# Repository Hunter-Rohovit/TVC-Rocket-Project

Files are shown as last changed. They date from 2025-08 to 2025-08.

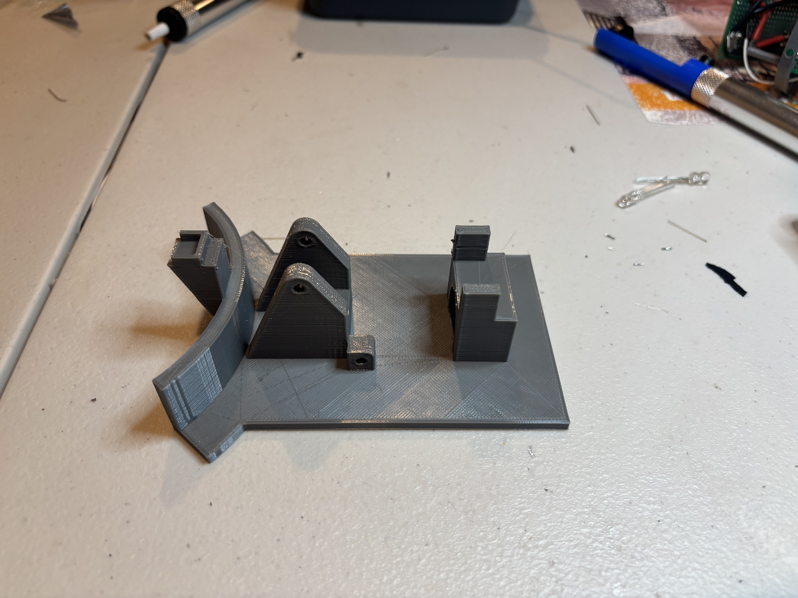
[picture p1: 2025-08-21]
Pictures_Videos/Launch Pad Assembly/IMG_3920.jpg

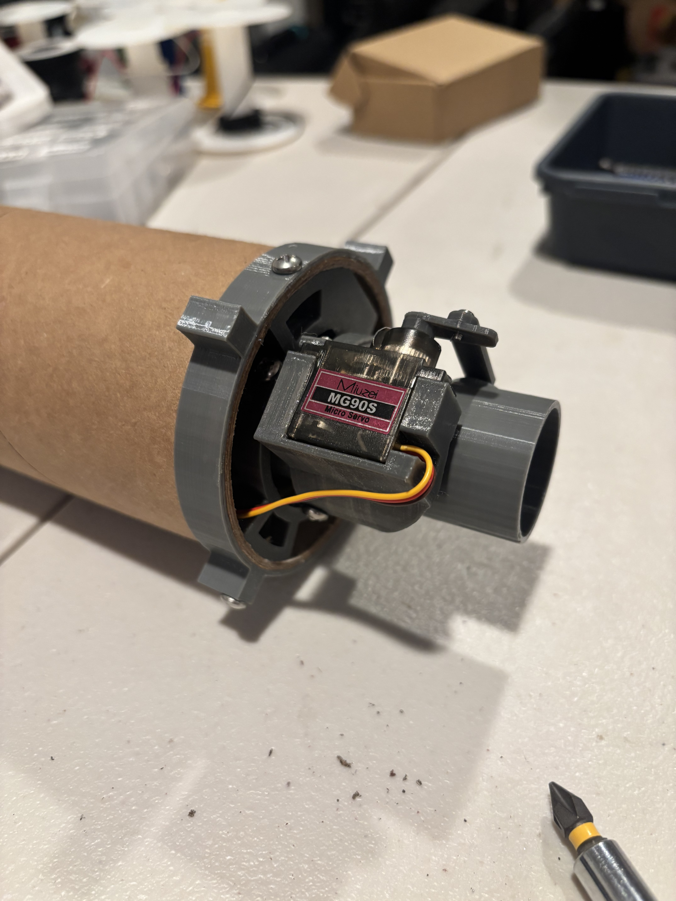
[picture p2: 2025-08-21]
Pictures_Videos/First Prototype Assembly/IMG_3949.jpg

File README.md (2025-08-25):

# Finless Thrust Vector Controlled Rocket
This page details the progress I have made in developing an autonomous Thrust Vector Controlled Model Rocket. This project was inspired by Joe Barnard at BPS Space, with his launching and landing of model rockets, as well as my own interest in Aerospace & Controls Engineering. It is a continuation of a project that began last summer (2024), where I designed the first prototype of a gimbal mount and ran a couple of tests while firing a motor. [Link](https://github.com/Hunter-Rohovit/TVC-Gimbal-Mount). All the work shown here was done over this summer (2025).

## Sections of this page:
1. [Overview](#overview)  
2. [CAD](#cad)  
3. [Avionics](#avionics)  
4. [Gimbal Mount](#gimbal-mount)  
5. [Servo Characterization](#servo-characterization)  
6. [Experimental Tests](#experimental-tests)  
7. [Computational Fluid Dynamics](#computational-fluid-dynamics)  
8. [6DoF Simulation in MATLAB](#6dof-simulation-in-matlab)  
9. [Control Algorithm](#control-algorithm)  
10. [Parachute Ejection & Recovery System](#parachute-ejection--recovery-system)  
11. [Launch Pad](#custom-launch-pad)

IMG_6904 (1)

---

## Overview
The goal of this project was to design, simulate, and build a finless rocket capable of stabilizing itself through thrust vectoring. This project integrates mechanical design, electronics, control theory, simulation, and experimental testing into a single system. Unfortunately, as the summer came to a close, I fell short of a first launch attempt by a couple of weeks. However, I made significant progress towards the eventual goal of launch and stable flight. Here's an overview of key accomplishments from this project so far: 
- Finalized design of gimbal mount and decreased thrust vector step size down to 0.2 degrees compared with the first prototype's step size of 0.75 degrees.
- Designed and assembled a custom flight computer Printed Circuit Board (PCB) consisting of a micro controller, Inertial Measurement Unit, Barometer Module, Data Storage, LoRa telemetry, and a MOSFET pyro channel.
- Used Solidworks CAD to design the rocket from scratch, integrating 3D printed mounts and other subsystems on the rocket.
- Developed a piston ejection system using 4Fg Black Powder for reliable deployment of parachutes.
- Designed and built a parachute to safely recover the vehicle during descent.
- Designed a custom Launch Pad with servo-driven quick-release Clamps, ignition circuit, and a custom Launch Pad PCB capable of controlling systems and transceiving radio commands.
- Computationally estimated and experimentally measured the rocket's Center of Gravity and Moment of Inertia about its lateral axes.
- Experimentally measured and analyzed servo motor hysteresis, latency, and response lag to accurately model gimbal mount dynamics.
- Formulated a nonlinear state-space representation of the rocket's rotational and translational dynamics in MATLAB.
- Built a full 6DoF state-space model of the rocket in MATLAB, integrating aerodynamic forces & moments, thrust vectoring, and environmental factors.
- Used Ansys Fluent's Computational Fluid Dynamics to determine lift and drag coefficients, aerodynamic moments, and center of pressure at various angles of attack to be used in 6DoF Simulation.
- Developed the structure of a Simulink Model integrating the 6DoF MATLAB function, a cascading PID Loop, and servo dynamics for accurate simulation and tuning of controller.
- Performed preliminary tuning and adjustment of PID gains of both inner and outer loops.
- Used C++ to program fundamental systems and tests of the Flight Computer, Launch Pad Computer, and Ground Station.

## CAD
Everything that was physically built was designed in Solidworks CAD beforehand. This includes the rocket, launch pad, and test stand. 
### Rocket
[Link To Onshape CAD Model of Rocket](https://cad.onshape.com/documents/63a8c4b73cd8738e99a4bd5d/w/619c465f67d6cd9f3f21c386/e/602e70b6c7c6c566dec7f707)


### Launch Pad
[Link To Onshape CAD Model of Launch Pad](https://cad.onshape.com/documents/538db86218341a015942f826/w/e10a91c609211941c8562602/e/c57fd2841c9af4f969e365a8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)


## Avionics
There were two custom Printed Circuit Boards built for this project. The first was for the flight computer and the second was for the launch pad computer. 
### Flight Computer
The flight computer consisted of a Teensy 4.0 Microcontroller, 5V and 3.3V Pololu Buck Converters, BNO085 Inertial Measurement Unit, BMP388 Barometer, SPI Flash SD, RFM95W Radio Transceiver, LED, Buzzer, external micro SD breakout, screw terminals for servo outputs, and a MOSFET circuit for a pyrotechnic ignition channel. I2C communication was primarily used for simplicity, though SPI communication was used for some devices.
#### Block Diagram
<p align="center">
  
</p>

#### Altium PCB Designer & Assembled PCB
<p align="center">
  
  
</p>

### Launch Pad Computer
The Launch Pad Computer consisted of a Teensy 4.0 Microcontroller, 5V Pololu Buck Converter, RFM95W Radio Transceiver, LEDs, Buzzer, 6 screw terminals for servo control (extra 2 for redundancy), 3 MOSFET circuits connected to Igniter Channels (2 extra channels for redundancy as well). 
#### Block Diagram
<p align="center">
  
</p>

#### Altium PCB Designer & Assembled PCB
<p align="center">
  
  
</p>

## Gimbal Mount
Having a robust gimbal mount that can effectively vector thrust is key to the success of this project, which is why I spent an entire summer dedicated just to it. The gimbal mount is controlled by two servo motors each connected to linkage mechanisms. There are two "loops". The inner loop is connected to the rocket motor case at a pivot, allowing the inner servo motor to rotate the motor case back and forth. The entire inner loop is connected to the outer loop by a pivot. The servo motor on the outer loop moves the inner loop back and forth in a direction perpendicular to the inner servo to allow vectoring in two directions. This mount has maximum and minimum vector angles of 4.5 degrees in both the pitch and yaw directions. 

While the final design of the gimbal mount is the same as the first prototypes in terms of how it vectors the thrust, these were some key changes made to improve the overall design:
- Shortened distance between control horn pivot and linkage connection.
- Increased distance between linkage connection and motor case/inner loop pivot.
- Increased support on inner and outer loops for more rigidity.
  
These three changes increased servo resolution and decreased flex in the mount. For more info, look at "Old TVC Mount Issues" folder.
[Link to Onshape CAD for Gimbal Mount](https://cad.onshape.com/documents/97e67a90e16df294bea9c07c/w/7f59de1ae6b53eca2492785b/e/3da8b51d2cceb306dbc743ae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)
<p align="center">
  
  
  
  
</p>

## Servo Characterization
In order to accurately represent the dynamics of the gimbal mount I needed an in depth understanding of how it moves when I command it to certain angles. This was one part of the project I hadn't anticipated needing to do, but as I began developing the Simulink Model, I realized it was very important. There are four characteristics of the servo I needed to understand it's dynamics:
1. Hysteresis (servos behave differently when commanded in different directions)
2. Latency (how much time it takes for the servo to begin moving once the command is called)
3. Response Lag (How long it takes for the servo to move to it's final position once the command is called)

### Servo Hysteresis
To accurately model this, I ran multiple tests increasing the servo angle from -22 to +22 degrees (max range of gimbal mount, corresponds to ~4.5 degrees actual) and decreasing from +22 to -22 degrees. 
I recorded the commanded angles and true angles and plotted them on graphs using MATLAB. I repeated this several times for both pitch and yaw axes. I then fitted a polynomial to the data. 
<p align="center">
  
  
  
  
</p>

### Servo Latency & Response Lag
To find these two values I used a camera to capture the motion of the gimbal mount. When I sent the signal to the servo motor, I simultaneously turned on the LED on the Flight Computer, so I could visually record the time stamp when command sent. From there I recorded the time stamp where the gimbal mount began moving (Latency) and recorded the time stamp where the gimbal mount stopped it's movement (Response Lag). I counted the number of frames between these three time stamps and divided by the frame rate to get the actual time. I repeated this for multiple tests to get several values at different angles.
<p align="center">
  
  
</p>

## Experimental Tests
To further understand the system, two important values needed to be found: the Center of Gravity and the Moment of Inertia about the lateral axes. I had estimated these values using Solidworks CG locator by overwriting the material density, finding the CG of each individual part, and finding their distance from the nose tip. However, the physical tests account for additional fasteners, glue, and wires that I didn't account for in the calculation, making it more accurate. 
### Center of Gravity
Finding the center of gravity was relatively simple. I hung a string and created a loop for the rocket to be placed. I shifted the rocket around until it was able to balance by itself and labeled that point the CG. 


### Moment of Inertia
To find the Moment of Inertia I used the Bifilar Pendulum Test. I hung two lines and attached them to the rocket 40 inches apart and centered about the CG, and recorded those measurements. I then rotated the rocket and started a timer as soon as I let go. After 10 oscillations, I recorded the time, to get the period of oscillation, and repeated this for multiple tests. From there, I could derive the Moment of Inertia from the mass of hte rocket, the length of the string, the distance between the two points, and the period time. I assumed the rocket to be symmetric about the longitudinal axis, so I only found one moment of inertia and used the same values for both Iy and Iz (pitch & yaw axes). I didn't find the roll Moment of Inertia as I could only control Pitcha and Yaw with Thrust Vectoring, and there wouldn't be any significant torques acting to roll the rocket. I still estimated it through a calculation, to be used in the 6DoF simulation.  
IMG_4121 (1)

## Computational Fluid Dynamics
Used Ansys Fluent CFD to deteremine coefficients of forces, moments, and the location of center of pressure at various angles of attack. Generated lift, drag, and moment coefficient curves across 0-90 degrees angle of attack. This data along with estimations for the aerodynamic damping derivative (derived from CFD results) was implemented into the MATLAB 6DoF function. For Lift and Drag Coefficients, Ansys was used to find the magnitude of these forces at 40m/s, which could then be used to solve for Cd x ReferenceArea and Cl x ReferenceArea rather than needing to calculate both Cd/Cl and reference area at different angles of attack. The static moment was normalized for velocity and CP location relative to CG. The center of pressure was defined from the nose tip and was calculated through dividing the static moment by the normal force to get the distance from CG. 

### 2D Simulation Velocity Contour
Ansys_Contour_Screenshot

### 3D Simulation Static Pressure Contour
Static Pressure Contour CFD

### CFD Results
<p align="center">
  
  
  
  
</p>

## 6DoF Simulation in MATLAB
Developed the equations for state space estimation and built a six-degree-of-freedom function in MATLAB to compute the time derivative of the rocket's 6DoF state. The state equation was formulated using quaternions and angular velocity for rotational motion, as well as inertial position and velocity to represent the rocket's translational motion. The choice of using quaternions over traditional euler angles was to prevent gimbal lock in the simulation. This function uses control inputs (vector angles), thrust data, aerodynamic data, and environmental conditions to estimate the translational and rotational acceleration. Aerodynamic forces and moments are computed in the body reference frame, then transformed into the inertial frame to integrate the full equations of motion. This simulation is fundamental to the development of the control algorithm and generation of flight profiles. 

### Visualization of Forces, Moments, and Axes 


## Control Algorithm
To develop the control algorithm I used Simulink to create a closed-loop model that integrates the 6DoF simulation from above and servo dynamics. The controller is structured as a cascaded PI-PID controller. The outer PI loop computes error based on attitude, and then outputs a desired angular rate. The inner loop then uses that output and the measured actual angular rate to calculate the error and generates commanded pitch and yaw outputs. The decision to use a PI rather than PID controller for the outer loop was based off the fact that the derivative of attitude error is angular rate, which is already being regulated in the inner loop. These commands then pass through a section that encapsulates the experimentally derived servo dynamics to feed the true thrust vector angles back into the process section. These were the Simulink Blocks used to model servo dynamics:
- Dead Zone: Very small changes to servo angle will not result in any change in servo position.
- Saturation: Maximum and minimum gimbal angles.
- Rate Limiter: Rising and falling slew rate of servo motor (maximum angular rate of motor).
- Transport Delay: Modeled servo latency
- Transfer Function: Used for servo response lag (the time to move from initial to final position)
- True Gimbal Function: Determines whether servo is moving up or down, and uses servo hysteresis data to ouput actual gimbal
- Zero-Order Hold: Models refresh rate of Inertial Measurement Unit (400hz)

Controller Tuning Strategy:
I have already completed preliminary tuning of this control algorithm, but some refinement is still needed. I started with the inner loop and then moved onto the outer loop, once the angular velocity showed convergence. The general strategy I used to tune both loops was to start with low Proportional gain and increase until I saw adequate response. If there were large-amplitude oscillations I increased the derivative gain, until it was less severe. If there was any steady-state offset I increased the integral gain. For both loops, I tuned one axis at a time, independently of one another. After, I modified the gains slightly when incorporating pitch and yaw together. In the future, I plan to add derivative filtering to the inner PID loop to prevent sharp spikes in commanded angles, and reduce the noise in the servo outputs.

### Simulink Model


### Scope Output

Example output including angular velocity, quaternions, desired pitch rate, commanded pitch rate. These scopes are what allowed visual tuning of the gains. There's significant noise in the commanded pitch angle showing the need for derivative filtering. 

## Parachute Ejection & Recovery System
The parachute ejection system on the TVC model rocket is a custom built piston ejection device. At the bottom of this system is the piston canister bulkhead. It is what stores the FFFFg black powder and the e-matches used to ignite it. The high pressure created by the ignition gases pushes out the piston cap, which in turn also pushes out the shock cord, parachute, and nosecone. This ejection method is significantly more reliable and easier to implement than a mechanical deployment device. It's also a lot lighter, helping with total mass reduction. The electronics are very simple, only requiring a single MOSFET pyro channel. For recovery, the parachute was designed for a 1kg rocket (actual mass is ~850g) to land at a velocity of 4m/s. It's made of ripstop nylon fabric, which is very strong and ligthweight. Attached to the shroud lines is a swivel to reduce the chances of lines tangling. Here's a video of the parachute ejection test: [Ejection Test](https://github.com/Hunter-Rohovit/TVC-Rocket-Project/blob/main/Pictures_Videos/Rocket%20Systems%20Tests/Parachute_Ejection_Test.mov)      
### Recovery System

### Assembly
<p align="center">
  
  
  
  
</p>

## Custom Launch Pad
The custom designed launch pad is composed of a spring loaded clamp release mechanism, a custom launch pad computer, and ignition circuit. In the secured position, the four clamps lock down onto the rocket's launch pad mount. Shortly after rocket motor ignition, the servo motors rotate and hit the release arms out from underneath the clamps, allowing the springs to snap downward. This design ensures the clamps retract quickly and remain out of the rocket's path. Here's a video releasing the launch clamps: [Launch Clamp Test](https://github.com/Hunter-Rohovit/TVC-Rocket-Project/blob/main/Pictures_Videos/Rocket%20Systems%20Tests/LaunchPadTest.mov)

### Clamped Position


### Open Position


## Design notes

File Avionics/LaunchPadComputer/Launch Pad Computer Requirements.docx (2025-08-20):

Purpose of the Launch Pad Computer:

- Remotely communicate with the rocket’s on board flight computer
- Remotely communicate with laptop ground station
- Fire rocket motor igniter
- Control servo motors for launch clamps

Needs of Launch Pad Computer:

- Microcontroller
- LoRa Radio Transceiver
- At least 2-3 MOSFET igniter circuits for redundancy
- 14.7V battery (what I have available already)
- 5V regulator for Teensy 4.0 and servo motors (must be capable of handing max stall current of 4 servo motors)
- Current regulation for firstfire mini motor starters (>3A)
- Pull down resistors on MOSFET circuits to prevent accidental firing
- Redundant arm switch

Resistor needed for the igniter circuit:

- Battery – 14.7V
- Recommended voltage: 12V
- Recommended current: >3A
- Using a 3.9 ohm resistor: 14.7/3.9 = 3.8 amps
- Power Dissipated: P=I^2*R = (3.8amps)^2*3.9ohms = 56W
  - Need a 3.9ohm resistor with high power dissipation (at least 60W)
  - https://www.digikey.com/en/products/detail/te-connectivity-passive-product/TE60B3R9J/2367245

Max Current Draw:

- Igniter: 2-5A
- Teensy 4.0: 250mA
- LoRa FRM95W radio: 100mA
- 4x MG90S servo: 900mA each

5V Regulator:

- Total current draw: 250mA+100Ma+900x4 mA = 3.95A
- It should be rated to 5A
- https://www.pololu.com/product/2851

Capacitors:

- The purpose for the capacitors on the MOSFET Igniter Circuits is to act as local energy reservoirs and avoid voltage dips when driving high current loads (e-match)
  - I chose 470 microfarad electrolytic capacitors based on the physical size of the capacitor and what I had available
  - Because the battery will be driving most of the current, I don’t need a super large capacitor, which is why 470 microfarads was good for what I needed
- The capacitors connected close to the servos are 220 microfarad capacitors
  - They serve a very similar purpose to prevent voltage dips and ensure the servos have enough power to be actuated all at the same time to release the launch clamps
- I could have done the actual calculation based on the allowable voltage drop using this equation: Voltage = I*dt/C or based on E=1/2*C*V^2
  - However, considering the energy required is an arbitrary value depending on how much is supplied by the battery, I decided not to use these equations to size the capacitors

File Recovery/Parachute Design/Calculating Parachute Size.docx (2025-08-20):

The main parameter I am designing around with the parachute is descent speed. Parachutes reach terminal velocity where the drag force from the parachute is equal to the dry weight of the rocket after burnout. We can use the drag force equation:

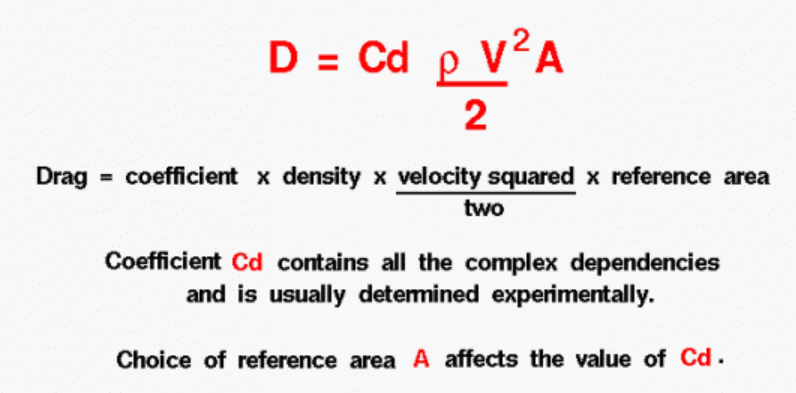
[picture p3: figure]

Coefficient of Drag for model rocket parachutes is estimated at 0.75 as per:

https://apogeerockets.com/education/downloads/Newsletter149.pdf

https://www.grc.nasa.gov/www/k-12/VirtualAero/BottleRocket/airplane/rktvrecv

The density of air at sea level ~1.225 kg/m^3.

Typical safe landing velocities are generally less than 6m/s. Apogee recommends 3.5-4.5 m/s.

- The decision for landing speed ultimately comes down to being soft enough to safely touch down without damaging any flight hardware while being small enough so that it doesn’t introduce any significant amount of mass.

The required drag force is equal to the force of gravity of the rocket, which we can calculate from the mass of the rocket. From there, the area of the parachute can be calculated.

It’s important to note that the area of the parachute should be the projected area not the surface area. However, these areas often do not vary by much and can be assumed to be the same.

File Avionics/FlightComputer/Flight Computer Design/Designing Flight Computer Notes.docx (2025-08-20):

- Teensy 4.0 doesn’t have on-board power management for switching between battery and usb power
  - I risk damaging usb ports in my computer if I have usb power and battery power plugged into the teensy at the same time
  - To fix this, we can cut the trace between the two 5V pads on the teensy to separate usb power from battery power.
  - The board will be powered through battery power, but will have comms through usb (for uploading software, etc.)
- Because we are using breakout boards for most of the modules, most of the boards have built-in voltage regulators, level shifting, and internal noise mitigation.
  - We don’t need to integrate pull-up or pull-down resistors or decoupling capacitors because most of it is already built in
  - These are plug and play or voltage driven meaning all I need to do is input the correct voltage and the devices will function properly
  - This makes my flight computer much simpler to build
- Teensy 4.0 doesn’t have a linear voltage regulator to drop input voltage from higher sources (9-12V) down to 5V
  - Need to input 5V meaning there will need to be a voltage regulator in our circuit
- Teensy 4.0 has a 3.3V out pin which allows at a maximum of 250mA
  - Almost all of the peripherals and sensors require 3.3V input and the total maximum current pulled through those devices at once exceeds 250mA
  - We will need a 3.3V source somewhere else in the circuit, which could also come from a 3.3V regulator
- We need a battery that is lightweight, high enough voltage (>5V, ideally more to account for voltage drop), and high enough current rated
  - The e-match circuit will pull significant current (~2A), so the battery must be able to pull that plus more at a minimum
  - 9V batteries don’t provide much current (500mA), even connecting them in parallel or in series only increases their total voltage or the amp-hour capacity
- The pyrotechnic igniter circuit requires a MOSFET over a relay because relays have mechanical switches in them which could accidentally be triggered by vibrations in the rocket
- The igniter circuit needs a bulk capacitor in parallel with the battery to mitigate voltage drop when igniter pulls significant current
  - Sensors and other peripheral devices will still be active during parachute deployment and we don’t want the voltage regulator to drop past it’s minimum voltage requirement
- Igniter circuit needs a pull-down resistor to prevent accidental triggering
  - The MOSFET gate can build up a small amount of capacitance containing charge that could cause the MOSFET to turn on unexpectedly
  - Pull-down resistor forces the gate to ground, keeping it off
  - Gate resistor between the MOSFET gate and GPIO pin on the Teensy is needed to prevent inrush current

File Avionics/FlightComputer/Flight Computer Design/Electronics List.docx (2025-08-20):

List of Basic Components Required for TVC:

- Microcontroller
- Inertial Measurement Unit (IMU)
- Barometer
- Data Recorder
- State Indicators
- Battery
- Parachute Stuff

Microcontrollers:

- Raspberry Pi
  - Pros:
    - High Processing Power (1-1.5ghz, 4-8 cores)
    - Built in Wi-Fi and Bluetooth for telemetry
    - Full Linux OS
    - Large community and support
  - Cons:
    - High power consumption
    - GPIO pins are controlled by the OS, which isn’t optimized for real time tasks, as control signals will have to pass through multiple layers of software before reaching the servos
    - Could be unpredictable timing in control loops, if OS decides to prioritize another process
    - It’s also kind of overkill processing power for what I need
- Beagle bone
  - Pros:
    - Real-time PRU (Programmable Real-Time Units) for precise control
    - High Processing Power (1 GHz)
    - Built in sensors like IMU, barometers, and motor drivers
    - Many GPIO pins and expansion options
    - Built-in battery management on some models
  - Cons:
    - More complex to program
    - Higher power draw
    - Bulkier than other microcontrollers
    - Fewer community resources
- Arduino Uno
  - Pros:
    - Very simple and beginner-friendly
    - Large community and wide library support
    - Low power consumption
    - Easy to program
    - Low cost
  - Cons:
    - Low processing speed (16MHz, 8 bit)
    - Limited RAM (2KB) and flash (32KB)
    - No built in IMU or wireless communication
    - Struggles with complex control algorithms
- Teensy 4.0/4.1
  - Pros:
    - Extremely high processing speed (60 MHZ, 32-bit)
    - Floating-point unit (FPU) for fast math calculations
    - Large RAM (1 MB) and flash (up to 8 MB)
    - High-resolution PWM
    - Compact size and low power consumption
    - Excellent library support
  - Cons:
    - Slightly more expensive than Arduino Boards
    - Fewer built-in peripherals (no Wi-Fi or Bluetooth)
    - Higher power draw than Arduino Uno/Nano
- Arduino Nano/Micro (Micro has more I/O pins)
  - Pros:
    - Very small and lightweight
    - Low power consumption
    - Inexpensive and widely available
    - Simple programming and wiring
  - Cons:
    - Low processing power (8-bit, 16 MHz)
    - Limited RAM (2KB) and flash (32 KB)
    - No built-in IMU

Overall Pick: Teensy 4.0

For it’s high processing power, high resolution PWM, compact size and lower power consumption. Fairly low priced, easier to program compared to some of the other boards, lots of resources online. I will need to integrate IMU sensors and telemetry modules as there isn’t built in Bluetooth or Wi-Fi.

Inertial Measurement Units:

- BNO055
  - Pros:
    - Integrated sensor algorithms
    - Easiest to use with basic microcontrollers
    - Includes magnetometer for absolute heading, reducing drift
    - Self-calibrating
    - 9 DOF
  - Cons:
    - Low update rate (100hz)
    - Higher latency due to on-board processing
    - Requires significant power
    - Less accurate due to internal processing limits
- BNO08x
  - Pros:
    - Advanced sensor algorithms with better drift correction
    - Higher output rates (1kHz)
    - Configurable algorithms for specific use cases
    - Better magnetic interference rejection
    - Lower power consumption than the BNO055
    - 9 DOF
  - Cons:
    - More complex setup and configuration
    - Requires more processing power
    - More expensive
- MPU 1650
  - Pros:
    - Super high sampling rates (32 kHz) and very low latency
    - Widely supported with good software libraries
    - DMP (Digital motion Processing) proesses raw gyroscope and accelerometer data to compute higher-level outputs like Euler angles or linear acceleration
  - Cons:
    - No absolute orientation without external magnetometer
    - More drift over time
    - More challenging to integrate without a dedicated fusion algorithm
- LSM6DS3
  - Pros:
    - Ultra-low power consumption
    - High output data rate (6.6 kHz)
    - Integrated finite state machine for custom algorithms
    - Small, lightweight
  - Cons:
    - No magnetometer (6 DOF)
    - More complex to implement advanced filtering and fusion
    - Higher data noise

Overall Pick: BN0O8x

I wanted to choose a 9DOF IMU which included a magnetometer to have better orientation accuracy and an absolute heading, which is critical for TVC control. This left me with either the BNO08x or the BNO055 as my options. However, the BNO055 has a data rate of only 100 Hz compared with the BNO08x of 1000Hz, which will be more suitable for real-time adjustments of the gimbal mount. In addition, this IMU includes integrated sensor fusion algorithms to provide orientation directly rather than requiring second-hand algorithms to derive the orientation. Although it is slightly more complex to set up and a slightly higher cost (manageable though), the overall flexibility and robustness of this IMU makes it the desired choice.

Barometers:

- MS5611
  - Pros:
    - Very high resolution (~10cm altitude resolution)
    - Low power consumption
    - SPI & I2C interfaces
  - Cons:
    - More expensive
    - Requires proper calibration and filtering for accurate results
- MPL3115A2
  - Pros:
    - Built-in altimeter function with altitude and temperature data
    - Mid resolution (30cm)
    - Low power consumption
    - Easy to integrate with microcontrollers
  - Cons:
    - Slow sampling rate (25hz)
- BMP388
  - Pros:
    - High resolution (8cm)
    - Fast data rate (200Hz)
    - Low power consumption
    - Built-in temperature compensation
  - Cons:
    - Requires careful calibration
    - More sensitive to temperature variations

Overall Pick: BMP388

Fast sampling and high resolution were the main reason why I chose this barometer. In addition to built-in temperature compensation functions and I2C and SPI interfaces, making it easy to integrate with the Teensy 4.0. The only cons is it can be sensitive to noise and requires careful calibration.

Types of Data Recorders:

- SD Card Modules
  - How it works:
    - Uses NAND Flash Memory where data is stored using floating gate transistors
    - Electrons are trapped to represent data, and stay trapped even when power is removed making it non-volatile
  - Pros:
    - High storage capacity compared to the others
    - Easy to obtain the data by simply removing the SD card
    - Widely supported across microcontrollers
  - Cons:
    - Physical interface and the mechanical connection of the SD card makes it more prone to flight vibrations
- Flash Memory Modules
  - How it works:
    - Very similar to SD card as it also uses NAND Flash Memory
    - Stores data using floating-gate transistors within a grid of memory cells
    - Cells act as switches controlling the flow of electricity to store binary data
    - Capable of storing multiple bits per cell allowing for high capacity in small form
    - It’s non-volatile meaning it doesn’t require power to store data
  - Pros:
    - High capacity
    - Fast read speeds
    - No moving parts making it resistant to vibrations
    - Simple integration with microcontrollers
  - Cons:
    - No standard file system (stores raw binary data)
    - More expensive than SD cards

Main difference between flash memory and SD cards is the mechanical vs. non-mechanical connection and built-in file system vs. raw binary data.

- FRAM (Ferroelectric RAM) Modules
  - How it works:
    - Data is written by applying an electric field across the ferroelectric capacitor
    - The direction of the polarization within the ferroelectric material represents the binary data
    - Main difference between FRAM and DRAM is DRAM stores data as an electrical charge in a capacitor.
  - Pros
    - Fast writing speeds
    - Non-volatile storage
    - not electromechanical making it resistant to vibrations
  - Cons:
    - Lower storage capacity

Overall Pick: Combination of FRAM module and SD Card module

Because the data on the SD Card is the most accessible out of all the options it makes the most sense to obtain the data from the SD Card. However, due to its mechanical connection, the data is sensitive to vibrations, which will inevitably occur during flight. The FRAM module being a non-volatile, solid-state device allows for high data recording rates with low noise. Compared with Flash memory, FRAM has near-instantaneous writes and is byte-addressable, so complex memory management isn’t needed. The one downside of using FRAM is the low storage capacity.

Calculate how much storage I would need

IMU Data: 6 axes (3D acceleration, 3D rotation) x 2 bytes per axis = 12 bytes

Barometer Data: 1 x 3 byte = 3 bytes

TVC Gimbal Angles: 2 angles x 2 bytes = 4 bytes

Gimbal Commands: 2 angles x 2 bytes = 4 bytes

Timestamp: 4 bytes

Flight Event Flags: 1 byte

Total: 28 bytes

Desired Sample Rate: 250hz

Bytes Per Second: 7000 bytes/s

Approximated Duration of Flight: 60 seconds

Total Storage Needed: 420,000 bytes

These are the modules we would use:

Adafruit SPI Non-Volatile FRAM Breakout - 4 Mbit / 512 KBytes - MB85RS4MT

Adafruit MicroSD breakout board PCB

Parachute Electronics: (will research more later, this is needed for sizing of the LiPo Battery)

- What do I need?
  - Something to command parachute deployment
  - a high-current switch to send a high current signal to the igniter
  - An e-match or nichrome wire to ignite the pyrotechnic charge
  - A redundant arming switch
- Microcontroller can be used to send signal to transistor
- For Switches:
  - Relay: electromechanical device that uses flowing current through a solenoid to create a magnetic field, which moves a mechanical switch. Allows us to switch from a low current signal from a microcontroller to high current for ignition of pyro charges
  - Relays in general are not a good idea to fly on rockets because the mechanical switch is prone to triggering due to vibrations
  - MOSFETS (Metal-Oxide-Semiconductor Field-Effect Transistor) is a type of transistor (used to amplify or switch electrical signals and power) that acts like an electronic switch.
  - They have very fast switching, high current capcity, and are solid-state so they are unaffected by vibrations of the rocket (much better option than the relays)
  - On a MOSFET there’s a gate that controls the flow of current through the MOSFET
    - The source is connected to ground and the drain is connected to the load (pyro igniter)
    - When the gate is activated a small voltage from the microcontroller creates an electric field which allows current to flow from the drain to the source

Telemetry:

- HiLetgo HC-12
  - Pros:
  - Cons:
- Adrafruit Feather M0 with RFM95
  - Pros:
  - Cons:
- Ebyte E32-433T30D

Summary:

Micrcontroller – Teensy 4.0

IMU – 2 x BN0O8x (one for recording gimbal angles, the other for rocket orientation)

Barometer - BMP388

Data Recorder - Adafruit SPI Non-Volatile FRAM Breakout - 4 Mbit / 512 KBytes - MB85RS4MT

+ Adafruit MicroSD breakout board PCB

Recovery – MOSFET + e-match or nichrome wire

Telemetry – 2 x Adafruit (PID 3072 RFM95W LoRa Radio Transceiver Breakout - 868 or 915 MHz (1 ground station, 1 on rocket)

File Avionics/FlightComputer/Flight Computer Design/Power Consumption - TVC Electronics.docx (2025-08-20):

Teensy 4.0: https://www.pjrc.com/store/teensy40.html

- Requires either 3.3 or 5V (will output either 3.3V or 5V)
- Max Current Draw: 100mA

BNO085: https://www.ceva-ip.com/wp-content/uploads/BNO080_085-Datasheet.pdf

- Voltage Requirement: 3.3V (2.4-3.6V)
- Max Current Draw: 15mA
- I2C or SPI capable

BMP388: https://www.bosch-sensortec.com/media/boschsensortec/downloads/datasheets/bst-bmp388-ds001.pdf

- Voltage Requirement: 3.3V or 5V
- Max Current Draw: 0.8mA
- I2C or SPI

Adafruit SPI Non-Volatile FRAM Breakout - 4 Mbit / 512 KBytes - MB85RS4MT: https://www.adafruit.com/product/4719

- Voltage Requirement: 3.3V or 5V
- Max current Draw: 2.6mA
- SPI only

Adafruit MicroSD breakout board PCB: https://www.adafruit.com/product/254#technical-details (https://www.adafruit.com/product/254%23technical-details)

- Voltage Requirement: 3.3V
- Current Draw (depends on the sd card): 50-100mA, up to 500mA: https://cdn-shop.adafruit.com/datasheets/TS16GUSDHC6.pdf
- SPI only

Recovery Electronics - MOSFET + e-match or nichrome wire

- E-matches need 3-12V, Nichrome Wire needs 6-12V
- E-matches pull 1-2A, Nichrome Wires pull 2-5A

Adafruit (PID 3072 RFM95W LoRa Radio Transceiver Breakout - 868 or 915 MHz: https://cdn-shop.adafruit.com/product-files/3179/sx1276_77_78_79.pdf

- Voltage Requirement: 3-5V
- 120mA max

MG90S Servos: https://makersportal.com/shop/mg90s-micro-servo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

- Voltage Requirement: 5V
- Current Draw: Operates between 70mA (no load) and 400mA (stall)

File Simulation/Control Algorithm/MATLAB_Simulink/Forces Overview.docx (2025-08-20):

To accurately simulate flight dynamics, I need a robust representation of all the forces on the rocket. Here’s the list of forces and torques that will be applied to the rocket during flight:

- Forces:
  - Thrust
  - Gravity
  - Aerodynamic Drag
  - Lift
  - Wind force
- Torques:
  - Gimbaled Thrust
  - Wind-induced Torque
  - Aerodynamic Damping Torque

I need a state vector to fully define the rocket’s dynamics including: orientation, angular rates, position, and translational velocity:

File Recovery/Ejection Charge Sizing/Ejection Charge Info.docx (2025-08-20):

Types of black powders used: All of them are very similar, main difference is the grain size, which effects burn timing.

- FFFFg (4Fg)
  - Very fine grain
  - Burns very fast
  - Used for small ejection charges on smaller model rockets
  - Very sensitive to ignition, so needs to be handled properly
- FFFg (3Fg)
  - Less fine grain
  - Burns slightly slower than 4Fg
  - Often used for a more controlled ejection to reduce overpressurization
  - Used on mid-sized rockets
- FFg (2Fg)
  - Larger grain
  - Burns slow
  - Used in large ejection wells

Most of the class A-F solid rocket motors use 4Fg black powder for their ejection charges, so I will stick with that for parachute deployment.

The calculation for the amount of black powder needed is fairly simple as it is just the ideal gas law:

Where:

- pressure can be changed to Force/Area
  - Where required force is an estimated value that changes with the mass of the nose cone and parachute, as well as how tight of a fit the nose cone has with the body tube
  - Area is the area of the body tube (**not the area of the canister containing the black powder**)
- Volume is the volume between the piston plate and the upper bulkhead.
- N is the molecular weight, which we can derive the mass of black powder from
- R is the gas constant of the combustion gases (266 lbf*in/lbm for 4Fg black powder)
- T is the temperature of the combustion gases (3307 R for 4Fg black powder)

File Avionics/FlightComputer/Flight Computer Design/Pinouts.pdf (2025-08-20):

Label | Pin # | Label | Pin # | Label | Pin #
Vin | 3.3V Line | Vin | 3.3V Line | Vin | 7.4V Line
GND | Ground Line | GND | Ground Line | GND | Ground Line
SCL | 13 | SCL | 13 | Vout | 5V Line
SDA | 12 | SDA | 12
INT | 2 | INT | 3
BT | n/a | BT | n/a | Label | Pin #
P0 | 3.3V Line | P0 | 3.3V Line | Vin | 7.4V Line
P1 | 3.3V Line | P1 | 3.3V Line | GND | Ground Line
RST | 23 | RST | 23 | Vout | 3.3V Line
DI | 11 | DI | 11 | EN | 17
CS | 10 | CS | 9
3Vo | n/a | 3Vo | n/a
| | | | Label | Pin #
| | | | Vin | 5V Line
Label | Pin # | Label | Pin # | GND | Ground Line
Vin | 3.3V Line | GND | Ground line | Control | 1
3Vo | n/a | VCC | 3.3V Line
GND | Ground Line | MISO | 12
SCK | 13 | MOSI | 11 | Label | Pin #
SDO | 12 | SCK | 13 | Vin | 5V Line
SDI | 11 | CS | 5 | GND | Ground Line
CS | 6 | | | Control | 0
Label | Pin # | Label | Pin # | Label | Pin #
Vin | 3.3V Line | Vin | 3.3V Line | GND | Ground Line
GND | Ground Line | 3V3 | n/a | R | 18
EN | 3.3V Line | GND | Ground line | G | 15
G0 | 4 | SCK | 13 | B | 14
SCK | 13 | MISO | 12
MISO | 12 | MOSI | 11
MOSI | 11 | CS | 8 | Label | Pin #
CS | 7 | !WP | n/a | Positive | 20
RST | 19 | !Hold | 3.3V Line | Negative Ground Line
Label | Pin # | Label | Pin #
Gate | 16 | Positive | 7.4V Line
Drain | E-match (neg) | Negative MOSFET drain
Source | Ground Line
| MOSFET | | E-match
BNO085 #1 | BNO085 #2
BMP388 | SD Card Module
Radio RFM95W | FRAM Module

Buzzer

5V Step Down Reg

3.3V Step Down Reg

Servo #2

Servo #1

RGB LED

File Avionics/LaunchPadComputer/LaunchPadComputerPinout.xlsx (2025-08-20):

5V Step Down Reg |  | RGB LED #1 |  | Igniter CH1
Label | Pin # | Label | Pin # | Label | Pin #
Vin | 14.7V Line | GND | Ground Line | Positive | 14.7V Line
GND | Ground Line | R | 20 | Negative | MOSFET CH1 drain
Vout | 5V Line | G | 19
 |  | B | 17 | Igniter CH2
Servo #1 |  |  |  | Label | Pin #
Label | Pin # | RGB LED #2 |  | Positive | 14.7V Line
Vin | 5V Line | Label | Pin # | Negative | MOSFET CH2 drain
GND | Ground Line | GND | Ground Line
Control | 4 | R | 23 | Igniter CH3
 |  | G | 22 | Label | Pin #
Servo #2 |  | B | 21 | Positive | 14.7V Line
Label | Pin # |  |  | Negative | MOSFET CH3 drain
Vin | 5V Line | Buzzer
GND | Ground Line | Label | Pin # | Switch
Control | 5 | Positive | 16 | Label | Pin #
 |  | Negative | Ground Line | Positive | High Power Resistor
Servo #3 |  |  |  | Negative | Igniter CH(1-3)
Label | Pin # | MOSFET CH1
Vin | 5V Line | Label | Pin # | High Power Dissipation Resistor
GND | Ground Line | Gate | 1 | Label | Pin #
Control | 6 | Drain | E-match (neg) | 1 | Switch
 |  | Source | Ground Line | 2 | Igniter
Servo #4 |  |  |  |  | **External to PCB
Label | Pin # | MOSFET CH2
Vin | 5V Line | Label | Pin #
GND | Ground Line | Gate | 2
Control | 14 | Drain | E-match (neg)
 |  | Source | Ground Line
Reserved Servo #1
Label | Pin # | MOSFET CH3
Vin | 5V Line | Label | Pin #
GND | Ground Line | Gate | 3
Control | 15 | Drain | E-match (neg)
 |  | Source | Ground Line
Reserved Servo #2
Label | Pin #
Vin | 5V Line |  |  | S
GND | Ground Line
Control | 18

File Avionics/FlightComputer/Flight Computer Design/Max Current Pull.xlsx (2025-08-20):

5V Reg |  | 5V Reg
Component | Max Current Draw (Amps) | Component | Max Current Draw (Amps)
Teensy 4.0 | 0.1 | IMU #1 | 0.1
Servo 1 | 0.4 | IMU #2 | 0.1
Servo 2 | 0.4 | FLASH | 0.02
Total | 0.9 | Barometer | 0.01
 |  | Radio | 0.14
 |  | SD card Breakout | 0.1
 |  | Total | 0.47

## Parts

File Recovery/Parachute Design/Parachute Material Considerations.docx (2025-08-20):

For parachutes the best choice materials need to be strong, thin, and flexible

- Needs to be strong so the parachute doesn’t rip
- Needs to be thin so that it’s lightweight
- A flexible parachute can be tightly packed and unfolds easier. It also allows for shock absorption when firing, reducing the risk of it snapping off during ejection

General materials used for smaller parachutes:

- Thin plastic sheets
- Mylar
- Plastic drop cloths
- Dry-cleaning bags
- Trash bags
- Gift wrapping plastic

For rockets with a mass greater than 300 grams use these types of materials: cotton, silk, polyester, or nylon

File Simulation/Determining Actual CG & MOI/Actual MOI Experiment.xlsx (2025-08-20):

Oscillation Tests |  |  |  | Moment of Inertia Calculation
Test # | Time (s) | Total Oscillations | Period (s) | Label | Value | Units
1 | 8.16 | 5 | 1.632 | Mass | 0.881 | kg
2 | 7.88 | 5 | 1.576 | Gravity Constant | 9.81 | m/s^2
3 | 7.96 | 5 | 1.592 | Period | 1.5976 | s
4 | 7.8 | 5 | 1.56 | Radial Distance | 14 | in
5 | 7.91 | 5 | 1.582 |  | 0.3556 | m
6 | 8.23 | 5 | 1.646 | String Length | 42.75 | in
7 | 15.75 | 10 | 1.575 |  | 1.08585 | m
8 | 15.95 | 10 | 1.595 | Moment of Inertia | 0.06507208492 | N*m
9 | 31.75 | 20 | 1.5875 |  | 222.3624645 | lbm*in^2
10 | 32.3 | 20 | 1.615
11 | 32.27 | 20 | 1.6135
 |  | Average Period | 1.5976
 |  | Standard Deviation | 0.02618405136
 |  |  |  | N*m | kg | in | m | Final MOI
 |  |  |  | 0.06507 | 0.04 | 16.26 | 0.413004 | 0.05824710784

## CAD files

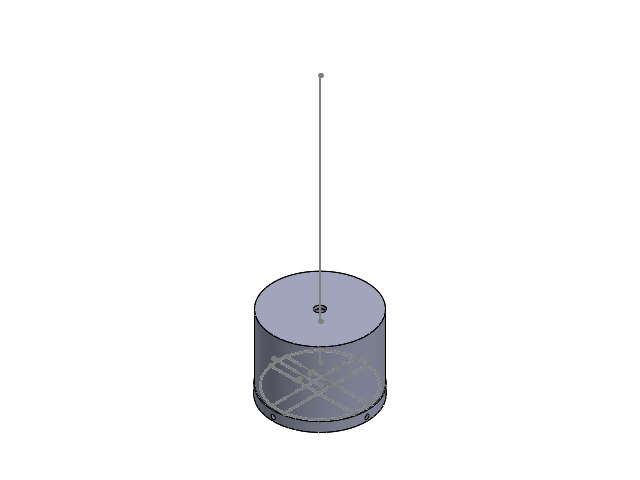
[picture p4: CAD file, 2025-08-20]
CAD/Recovery/Piston Ejection System.SLDASM
Piston Canister Bulkhead
Piston Cap
PistonTubeCoupler

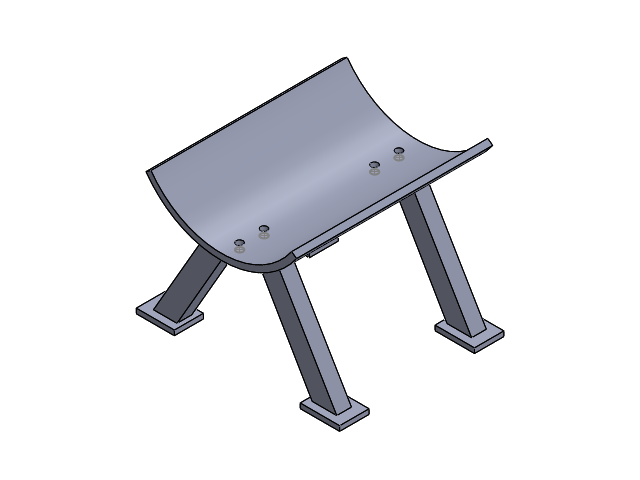
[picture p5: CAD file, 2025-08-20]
CAD/Other/RocketHolderAssembly.SLDASM
Rocket Holder
RocketHolderLegs x 2

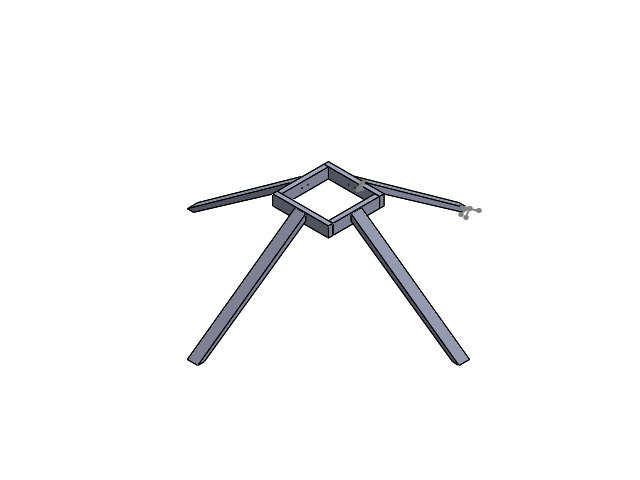
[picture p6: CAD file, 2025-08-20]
CAD/TestStand/TestStandFrame.SLDASM
2x4^TestStandFrame
Copy of 2x4^TestStandFrame
2x4(2)^TestStandFrame x 2
Angled2x4^TestStandFrame x 4

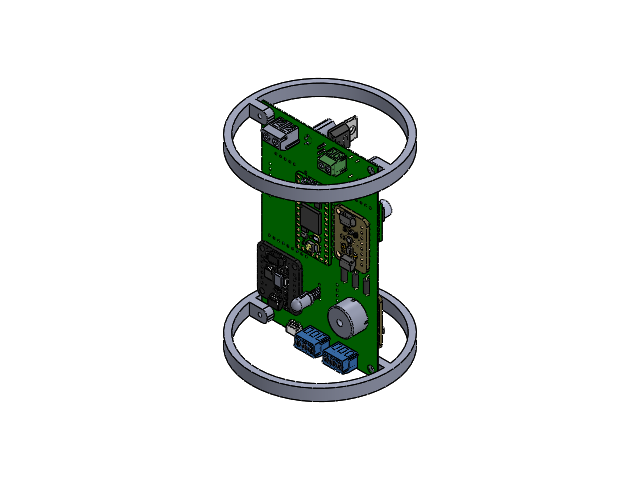
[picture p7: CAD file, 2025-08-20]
CAD/Flight Computer/FlightComputerPCB/FlightComputerPCB.SLDASM
DEV-15583 board
C5-C18 (0.55mm)
C20-C24 (0.65)
R1-R3 (0.4inch)_1269AS-H-3R3M=P2
L1^DEV-15583 ASS
C x 2
C2
SM4B-SRSS-TB
Capacitor
QFN 28 v2
SMD Crystal v1
CAP 0403 v1 x 8
CAP Ceramic 0403 v1 x 8
Res 0403 v1 x 4
CAP ML 0403 v1 x 5
SOT-323 v1
Inductor SMD 0403 v1 x 5
SOT-363 v1
SOT23-5 v1
CAP 0805 T095 v1 x 2
CAP 0805 T075 v1
TSSOP16 v1
RES 0805 v1 x 3
Board
0603-NO x 4
SOD-323
BMP388_1
0805-NO x 2
SOT23-5
RESPACK_4X0603
SOT363
JST_SH4 x 2
CHIPLED_0603_NOOUTLINE
6912141100xx_CAGE x 2
6912141100xx_PIN x 2
6912141100xx_VIS x 2
speaker
Lente^Led RGB 5mm
Terminais^Led RGB 5mm
Printed Circuit Board
BNO055-9axis-IMU v2
BNO085-9axis-IMU v1
BODY-TSSOP
LEAD-TSSOP x 16
Crystal_XTAL3215_32.768KHz v2
SOT23-5 v1_2
BSS138PS v2
LED 0603 single color v1
CAPC-0805-T0.95-BN v1 x 2
CAPC-0603-T0.9-BN v1 x 5
YC164_RESPACK v1 x 3
qwicc v1 x 2
d24v25fx-step-down-voltage-regulator (3) x 2
6911031100xx_CAGE x 6
6911031100xx_PIN x 6
6911031100xx_VIS x 6
Board_2
MICROSD
0805-NO_2
0603-NO_2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

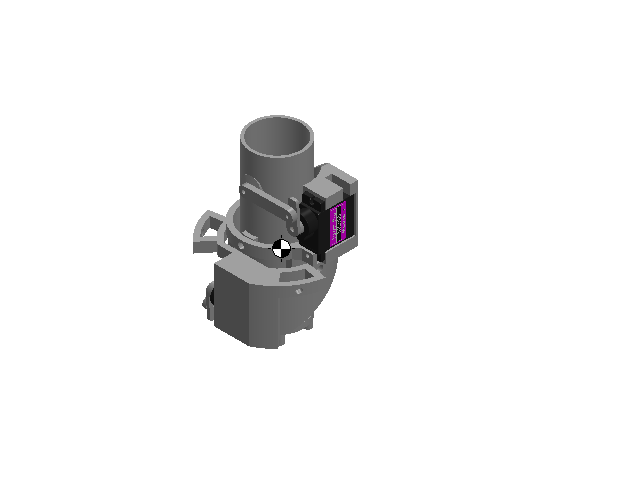
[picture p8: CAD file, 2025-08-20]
CAD/TVC Mount/TVC Mount V2.SLDASM
Inner Loop
MG90S Servo x 2
Outer Loop V2
TVC Motor Case
ControlHorn x 2
Linkage 1 V2
Linkage 2 V2

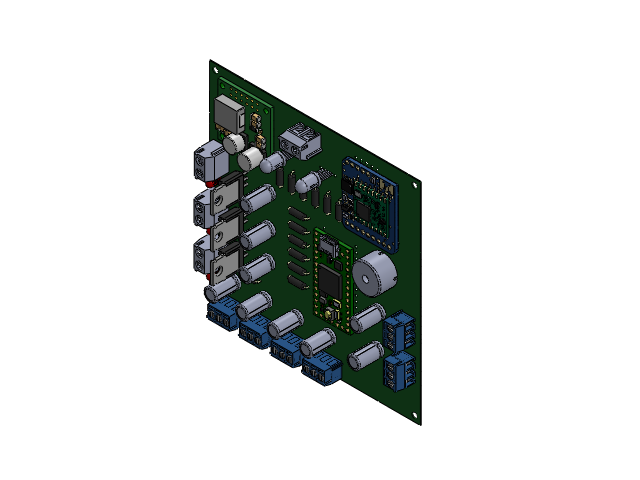
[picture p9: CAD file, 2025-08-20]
CAD/LaunchPad/LaunchPadComputer.SLDASM
Extruded x 3
Extruded-12 x 3
Extruded-13 x 3
Extruded-15 x 3
Extruded-16 x 3
Lente^Led RGB 5mm x 2
Terminais^Led RGB 5mm x 2
6911031100xx_CAGE x 18
6911031100xx_PIN x 18
6911031100xx_VIS x 18
SM4B-SRSS-TB
pins x 3
logo x 3
DEV-15583 board
C5-C18 (0.55mm)
C20-C24 (0.65)
R1-R3 (0.4inch)_1269AS-H-3R3M=P2
L1^DEV-15583 ASS
C x 2
C2
QFN 28 v2
SMD Crystal v1
CAP 0403 v1 x 8
CAP Ceramic 0403 v1 x 8
Res 0403 v1 x 4
CAP ML 0403 v1 x 5
SOT-323 v1
Inductor SMD 0403 v1 x 5
SOT-363 v1
SOT23-5 v1
CAP 0805 T095 v1 x 2
CAP 0805 T075 v1
TSSOP16 v1
RES 0805 v1 x 3
d42v55fx-step-down-voltage-regulator

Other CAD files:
CAD/Flight Computer/FlightComputerPCB/C1.SLDASM
CAD/Flight Computer/FlightComputerPCB/Led RGB 5mm.SLDASM
CAD/LaunchPad/4.SLDASM
CAD/LaunchPad/6.SLDASM
CAD/LaunchPad/R5.SLDASM
CAD/Flight Computer/FlightComputerPCB/__9.SLDASM
CAD/LaunchPad/R2.SLDASM
CAD/Flight Computer/FlightComputerPCB/MOSFET_1.SLDASM
CAD/LaunchPad/1.SLDASM
CAD/LaunchPad/R10.SLDASM
CAD/Flight Computer/FlightComputerPCB/RFM95 v1.SLDASM
CAD/Flight Computer/FlightComputerPCB/U_.SLDASM
CAD/Flight Computer/FlightComputerPCB/0603-NO.SLDPRT
CAD/Flight Computer/FlightComputerPCB/0603-NO_2.SLDPRT
CAD/Flight Computer/FlightComputerPCB/0805-NO.SLDPRT
CAD/Flight Computer/FlightComputerPCB/0805-NO_2.SLDPRT
CAD/Flight Computer/FlightComputerPCB/1776244-2.SLDPRT
CAD/Flight Computer/FlightComputerPCB/4682 Micro SD Breakout.SLDASM
CAD/Flight Computer/FlightComputerPCB/4816 BMP390 QT.SLDASM
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

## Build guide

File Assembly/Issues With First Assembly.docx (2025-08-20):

Changes that need occur for the next rocket assembly: (detailed instructions and changes for how the rocket should be put together is in another document)

- 27in body tube length
  - Transitioning to a 30in body tube length for a greater MOI, better passive stability, and slightly higher static margin, with the cost of slightly less control authority though still very high (303 degrees/s^2 vs 340 degrees/s^2 max angular acceleration due to thrust vectoring) as well as a slight reduction in estimated max height (about 10 meters less)
  - Cutting down the tube using the miter saw should be done again as it had a very clean cut
- Retaining rings could increase in diameter about 0.2-0.3mm
  - They fit fairly well, but there were some gaps between the rings and the cardboard tube which made the superglue ineffective.
- Battery and flight computer mounts should decrease in diameter about 0.2-0.3mm
  - These components originally fit very well, but when super glue was applied to the retaining rings it became extremely difficult to get the mounts to fit
  - I want a tighter fitting piston canister bulkhead to prevent any gas escaping through a looser fit
- Launch pad mount needs to be modified to be stronger and to fit with the smaller diameter cardboard tube

New Pieces to 3D print:

- Larger nosecone bulkhead
- Larger diameter retaining rings
- Smaller diameter battery and computer mounts
- New piston canister bulkhead (other one was used in parachute ejection test)
- Upgraded test stand mount
- New launch pad mount

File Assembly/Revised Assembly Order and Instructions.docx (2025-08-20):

TVC Gimbal & Launch Mount Assembly: (Launch Mount is used as a reference point, which is why it should be assembled first)

- Put superglue on the inside of the launch pad mount
- Place the launch pad mount over the cardboard tube so that the bottom of it is flush with the bottom of the tube and let it dry
- Where there is already holes in the mount, drill holes in the cardboard tube
- Fasten the gimbal mount to the launch pad mount and cardboard tube
  - Make sure the IMU and servo cables are running up the rocket tube
  - Can also attach the TVC gimbal mount later

Middle Section Assembly:

- Use a ruler again to measure from top of body tube down to 8.35in (start of access panel)
  - Mark that distance on the side where the launch pad mount has a bolt in it (reference point)
  - Draw a circle using the flexible ruler around the tube at that mark.
- Draw another circle 8.85in down from the first circle
- Draw 4 lines from one circle to the other using a straight edge from the four launch pad mounts as reference points
- From the reference mount draw a straight line between both circles
- On the line attached to the reference mount and the line opposite of that, drill 5 holes (1/8in drill bit):
1) 0.125in up from top circle
2) 0.25 in down from top circle
3) 3.79in down from first hole
4) 0.75in down from second hole
5) 3.72in down from third hole
- On the two lines 90 degrees from the line with the holes, cut along the lines using utility knife to create the access panel
  - The access panel should open opposite of the reference point
  - It’s best to cut slightly below the lines than above the lines (i.e. make the access panel larger than 180 degrees around the tube)
- Place the piston canister bulkhead’s retaining ring flush with the top of the opening for the access panel and attach fasteners to the top and bottom holes
  - Cut the next two holes 90 degrees from the first two, either using the drawn line as a reference point or poking a hole using an ice pick where there’s a hole in the retaining ring
  - Put fasteners in those two holes
  - After checking all fasteners are in the right spot, take them all out once again, apply super glue to the retaining ring and place it in the correct spot
  - Put the fasteners in immediately after to secure it when drying
- Fasten the retaining rings to their respective bottom holes
  - Use the ice pick to poke a small hole in the offset angle holes
  - Drill holes in those spots
  - Attach fasteners to those bolts
- With the 3 fasteners attached to each, put the access panel on top and try attaching fasteners to ensure holes are in the correct spots
  - If they are in the right spots, take off the access panel, leave 3 fasteners in each bolt and put superglue on all of the retaining rings
- Once all of those are dry, the test stand mount can be attached
  - First, determine the actual CG of the rocket with everything attached (as if it were flight ready)
  - Mark that location on the bottom line (should be somewhere around the flight computer)
  - Drill a hole at that mark
  - Attach the retaining ring
  - Use the ice pick to mark and drill new holes in those spots
  - Take the fasteners out, super glue the outsides of the ring then reattach to its position and let dry
- When actually using the launch pad mount on the outside of the tube:
  - all fasteners will need to be removed from the rocket, so that it can slide down the tube
  - then put the access panel into place and fasten everything down.
- Once all retaining rings are put into place, the other two sections can be put into place.
  - Launch pad mount

Nosecone & Recovery Section Assembly:

- Create a knot in one end of the shock cord
- Attach the knot to the loop bracket on the piston canister bulkhead and fasten the bracket down
- Slide the shock cord through the tube
- Tie another knot and attach to the nosecone bulkhead’s loop bracket
- Superglue the nosecone bulkhead to the nosecone
- Attach a clip from the loop attached to the nosecone to the parachute swivel
- Put the piston cap on top of the piston canister bulkhead before inserting into the rocket, so that it’s in the right position
- Fasten the piston canister bulkhead to its retaining ring
- Pack the shock cord and parachute into the storage area
- Put tape around the bottom of the nose cone for a tight fit and connect the nose cone to the tube

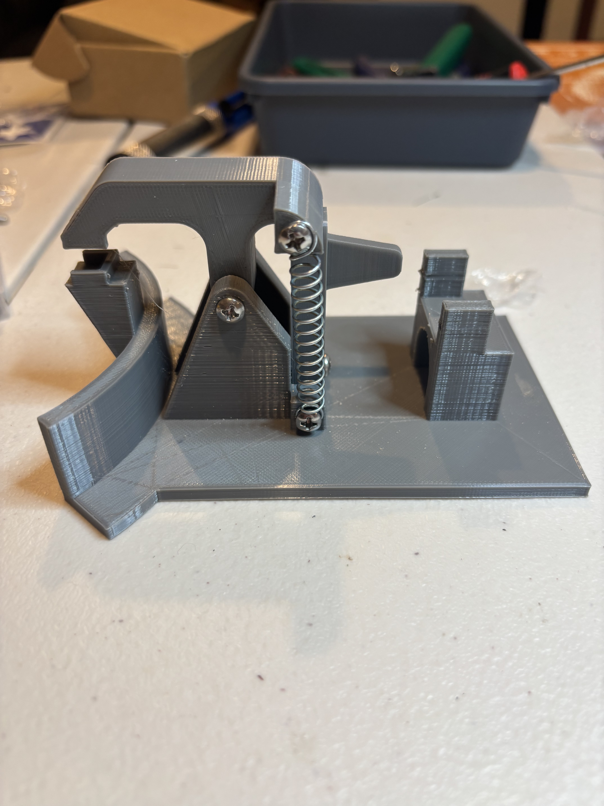
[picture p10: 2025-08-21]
Pictures_Videos/Launch Pad Assembly/IMG_3925.jpg

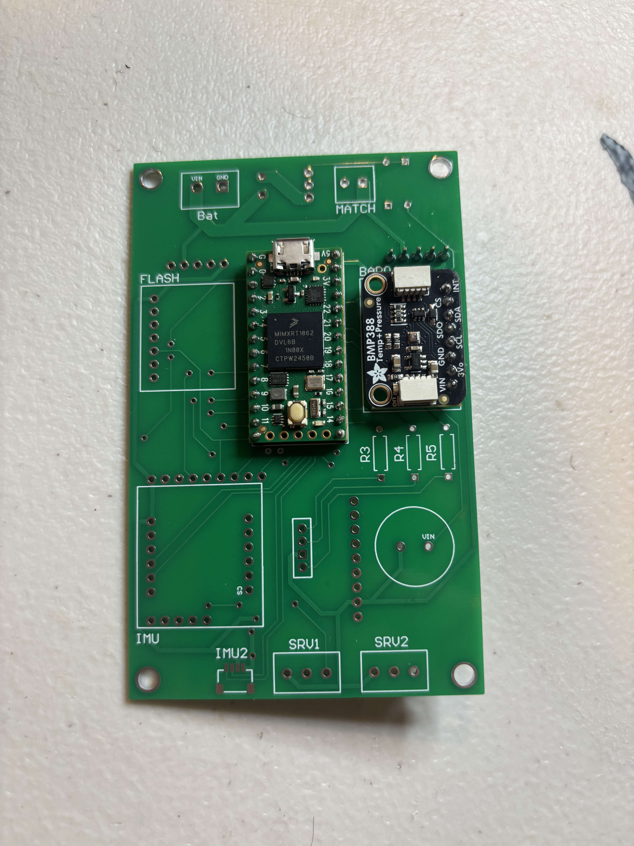
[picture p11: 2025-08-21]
Pictures_Videos/Flight Computer Assembly/IMG_3888.jpg

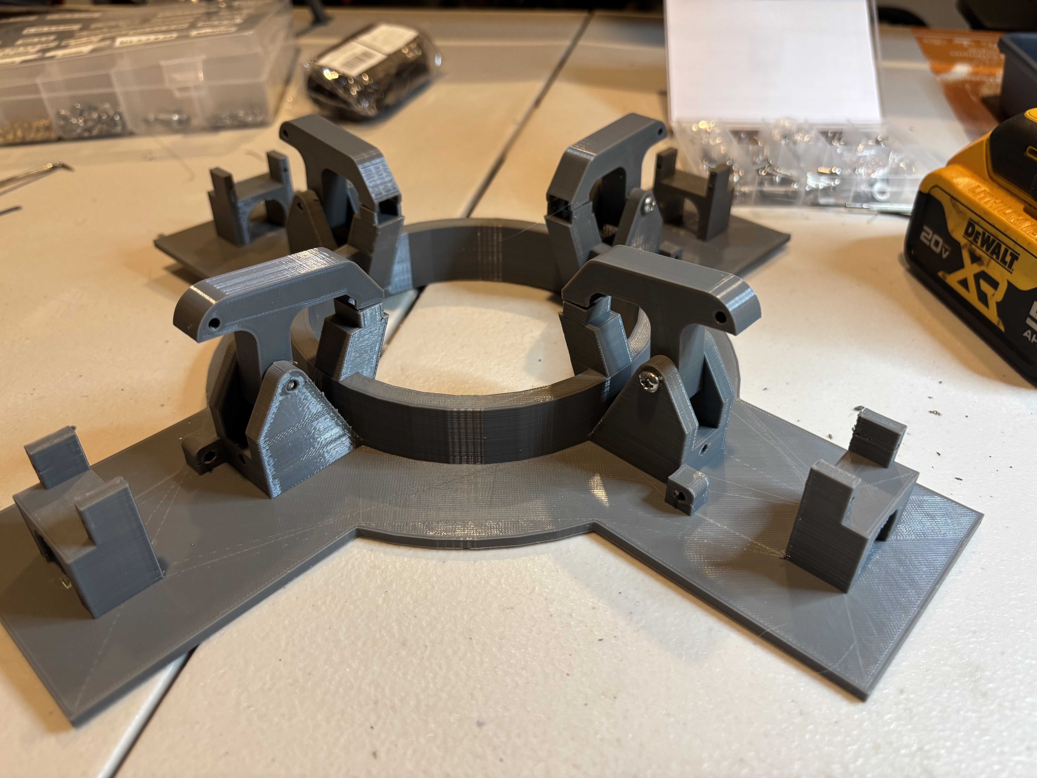
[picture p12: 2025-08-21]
Pictures_Videos/Launch Pad Assembly/IMG_3960.jpg

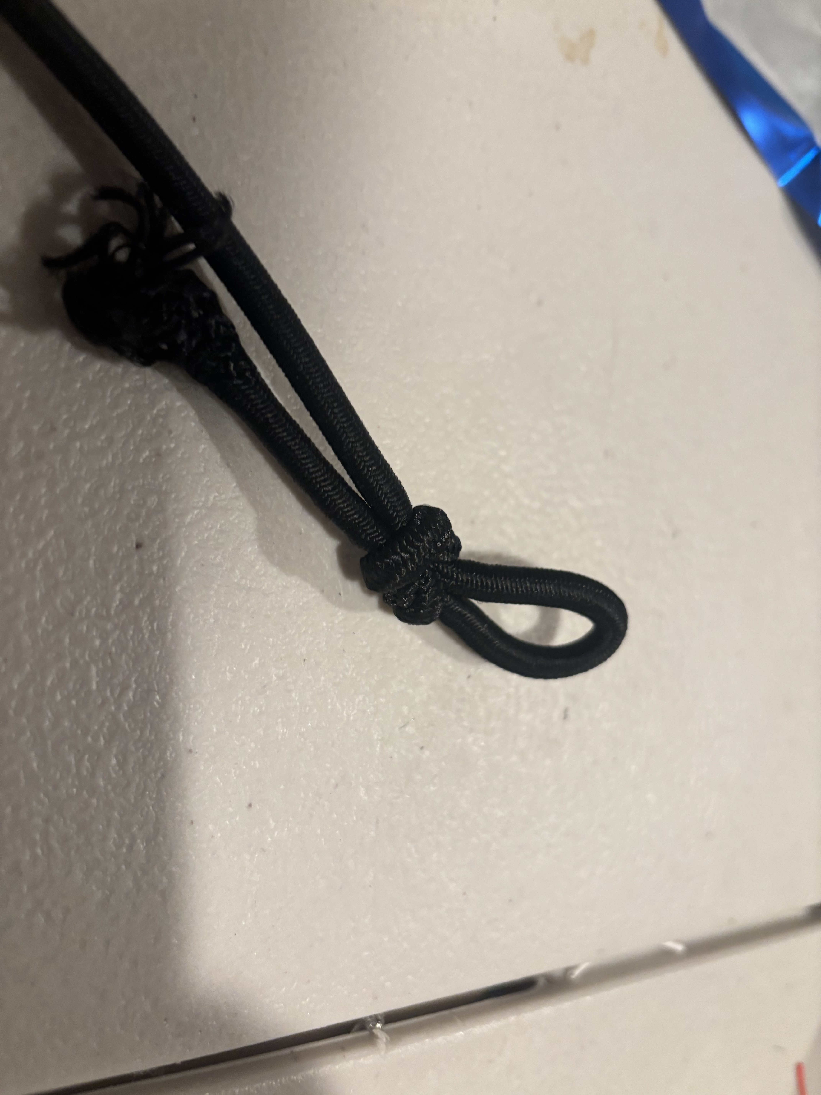
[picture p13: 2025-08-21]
Pictures_Videos/First Prototype Assembly/IMG_4007.jpg

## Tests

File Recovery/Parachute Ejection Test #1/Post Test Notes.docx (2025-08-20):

First test of the parachute piston ejection system completed without any serious damage to the rocket or unexpected behavior of the system. Generally, I would call it a success. Here are some notes:

- Parachute and nose cone ejected vertically in the air and reached max shock cord length
- No visible signs of any damage caused by the gun powder to the rocket
- Lots of soot between the piston canister bulkhead and piston cap, which is to be expected
- There were not significant amounts of soot in any other areas, especially critical regions including the flight computer or battery storage
  - There was a trace amount in the parachute storage section, but nothing to be concerned about
- Piston cap did not eject from the rocket tube as I was expecting
  - Not super critical as the rest of the system performed as expected
  - There was a decent amount of tape around the piston cap which could have prevented it from moving
  - Black powder gases likely escaped through gaps between shock cord and piston cap or piston cap and body tube
  - Next test I will try it without tape
- There was a flame that went out the side of the rocket right where the piston canister bulkhead was mounted
  - I’m not sure where those gases escaped from as there’s no sign of any holes created or leaks
  - My guess is that it escaped from the removeable access panel (a tiny cardboard cut out section allowing me to access flight computer and battery)
  - There was a very small amount of discoloration on the outside of the battery mount, which I assume is where it escaped
  - Didn’t cause any sort of failure and didn’t pose a threat to critical areas, but still an area of concern for next test
  - Need to ensure a better seal with the super glue on the piston canister bulkhead’s retaining ring
- Could probably use slightly less gunpowder
  - I filled both of the canisters about ¾ full with black powder, which was well more than sufficient
  - I could probably fill them up halfway next time
- Parachute was deployed by the time the shock cord snapped back meaning the packing was good

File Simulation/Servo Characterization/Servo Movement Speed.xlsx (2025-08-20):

 | delta_angle | start |  | stop |  | frames | time | angular rate (degrees/sec)
Yaw | 44 | 8:19 | 259 | 9:19 | 289 | 30 | 0.125 | 352
Yaw | 44 | 11:06 | 336 | 12:05 | 365 | 29 | 0.1208333333 | 364.137931
Yaw | 44 | 7:16 | 226 | 8:18 | 258 | 32 | 0.1333333333 | 330
Yaw | 44 | 12:16 | 376 | 13:16 | 406 | 30 | 0.125 | 352
Pitch | 44 | 12:03 | 363 | 13:02 | 392 | 29 | 0.1208333333 | 364.137931
Pitch | 44 | 30:10 | 910 | 31:10 | 940 | 30 | 0.125 | 352
Pitch | 44 | 2:13 | 73 | 3:09 | 99 | 26 | 0.1083333333 | 406.1538462
 |  |  |  |  |  |  |  | **Conservative underestimate of angular rate is ~320-330 degrees/sec
 |  |  |  |  |  |  |  | **will use that value in simulink

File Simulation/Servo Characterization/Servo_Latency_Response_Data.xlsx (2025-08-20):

Axis | Delta Angle | Light On Time | Light On Frame | First Move Time | First Move Frame | Stop Move Time | Stop Move Frame | Latency (ms) | Response Time (ms) | Total Lag (ms)
Pitch | 22 | 2:29 | 89 | 3:11 | 101 | 4:03 | 123 | 50.00 | 91.67 | 141.67
Pitch | 22 | 42:23 | 1283 | 43:02 | 1292 | 44:00 | 1320 | 37.50 | 116.67 | 154.17
Pitch | 22 | 14:29 | 449 | 15:11 | 461 | 16:04 | 484 | 50.00 | 95.83 | 145.83
Pitch | 15 | 49:07 | 1477 | 49:20 | 1490 | 50:09 | 1509 | 54.17 | 79.17 | 133.33
Pitch | 15 | 18:29 | 569 | 19:08 | 578 | 19:24 | 594 | 37.50 | 66.67 | 104.17
Pitch | 15 | 47:13 | 1423 | 47:27 | 1437 | 48:14 | 1454 | 58.33 | 70.83 | 129.17
Pitch | 10 | 15:18 | 468 | 15:28 | 478 | 16:14 | 494 | 41.67 | 66.67 | 108.33
Pitch | 10 | 41:27 | 1257 | 42:10 | 1270 | 42:17 | 1277 | 54.17 | 29.17 | 83.33
Pitch | 10 | 8:26 | 266 | 9:10 | 280 | 9:19 | 289 | 58.33 | 37.50 | 95.83
Pitch | 5 | 38:06 | 1146 | 38:20 | 1160 | 38:26 | 1166 | 58.33 | 25.00 | 83.33
Pitch | 5 | 6:03 | 183 | 6:16 | 196 | 6:22 | 202 | 54.17 | 25.00 | 79.17
Pitch | 5 | 32:13 | 973 | 32:27 | 987 | 33:04 | 994 | 58.33 | 29.17 | 87.50
Pitch | -22 | 2:27 | 87 | 3:09 | 99 | 3:25 | 115 | 50.00 | 66.67 | 116.67
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

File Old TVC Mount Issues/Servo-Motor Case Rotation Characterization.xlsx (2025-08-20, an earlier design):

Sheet: Sheet1
TVC Mount 1 (X-axis) |  |  |  |  |  | TVC Mount 1 (Y-axis)
Control Arm Length (L) | 0.33 | 0.33 | 0.33 | 0.33 | in | Control Arm Length (L) | 0.33 | 0.33 | 0.33 | 0.33 | in
Distance From Point of Rotation (R) | 1.123 | 0.679 | 0.679 | 0.679 | in | Distance From Point of Rotation (R) | 1.106 | 1.11 | 1.11 | 1.11 | in
Angle of Servo (θ) | 10 | 5 | 15 | -12 | Degrees | Angle of Servo (θ) | 10 | 5 | 15 | -12 | Degrees
 | 0.1745329252 | 0.0872664626 | 0.2617993878 | -0.2094395102 | Radians |  | 0.1745329252 | 0.0872664626 | 0.2617993878 | -0.2094395102 | Radians
Predicted Angle of Motor Case (ϕ) | 0.05104968465 | 0.04237113824 | 0.1261224461 | -0.1012196701 | Degrees | Predicted Angle of Motor Case (ϕ) | -0.05183505249 | -0.02591406705 | -0.07702233508 | 0.06185101188 | Degrees
 | 2.924931476 | 2.427687394 | 7.226283861 | -5.799459902 | Degrees |  | -2.969929739 | -1.484766672 | -4.413054728 | 3.543801939 | Degrees
Actual Angle of Motor Case (ϕ) | 4.795 | 2.346 | 7.207 | -5.725 | Degrees | Actual Angle of Motor Case (ϕ) |  |  |  |  | Degrees
 | TVC Mount 1
 | θ | ϕ X (predicted) | ϕ Y (predicted)
 | -15 | -4.3619 | -4.4290
 | -14 | -4.0766 | -4.1394
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

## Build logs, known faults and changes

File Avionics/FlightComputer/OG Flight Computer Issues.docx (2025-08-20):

- Realized CLK and MISO pins were shorted after probing SD card module pins with the DMM’s continuity test
  - Fairly easy fix as there was wire sticking up through one of the protoboards from the CLK pins touching the MISO rail
  - I cut those wires, probed CLK and MISO again and saw no signs of a short
- I was able to connect to the servos, RGB LED, and buzzer through the flight computer, but ran into issues with all devices using SPI communication
  - I first noticed this issue trying to initialize the 1st BNO085 sensor where the serial terminal would freeze after “starting BNO085 test”.
  - I thought initially it was an issue with the serial terminal and the usb cable not allowing transfer of data to it, but I was able to resolve the serial terminal issue by restarting the teensy and matching the baud rates of my code files. However, it was still freezing.
  - I realized, the microcontroller was either freezing or crashing when I called BNO085.begin_SPI(BNO085_CS), suggesting something was preventing SPI communication from initializing
  - The most common reason for this is incorrect wiring of the pins, pins disconnected, or pins being shorted. To figure out if this was the case I probed all pins with my multimeter to verify they were corrected to the correct teensy pins. I also probed the pins within the BNO085 board to ensure there wasn’t any shorts. After doing this all wiring seemed to be correct and there weren’t any signs of shorts
  - It also could have been an issue with improper voltage supply and grounding, but I probed between the modules ground pins and vin pins and got a voltage of 3.3V, which is correct
  - I also tried other boards like the 2nd BNO085 and the BMP388 and ran into the same exact issue, which suggests this is very likely an SPI communication issue (which I already knew)
  - Because of the fact that the wiring appeared correct, there were a couple of issues I had considered:
    - There could be bus contention issues where multiple devices are trying to drive the miso line. I changed my code to pull all cs pins high except for the one I’m trying to communicate with, which didn’t fix anything (I figured this would be the case as Adafruit’s breakout boards have an internal pullup resistor on each of the CS pins).
    - There are probably one or multiple SPI devices interfering with MISO. Other people have had issues especially with SD modules and IMU sensors that cause conflict on the SPI bus. To debug this, I will disconnect all MISO lines except for the one I want to try and connect to and see if this is the issue
    - This could also just be an issue of the wires being connected enough to appear as continuous on the multimeter, but not enough for continuous operation of the modules

All of these issues were resolved by switching to a PCB and changing most of the SPI communication to I2C. Although slightly slower, the simplicity of I2C makes it much less prone to errors and bus conflicts.

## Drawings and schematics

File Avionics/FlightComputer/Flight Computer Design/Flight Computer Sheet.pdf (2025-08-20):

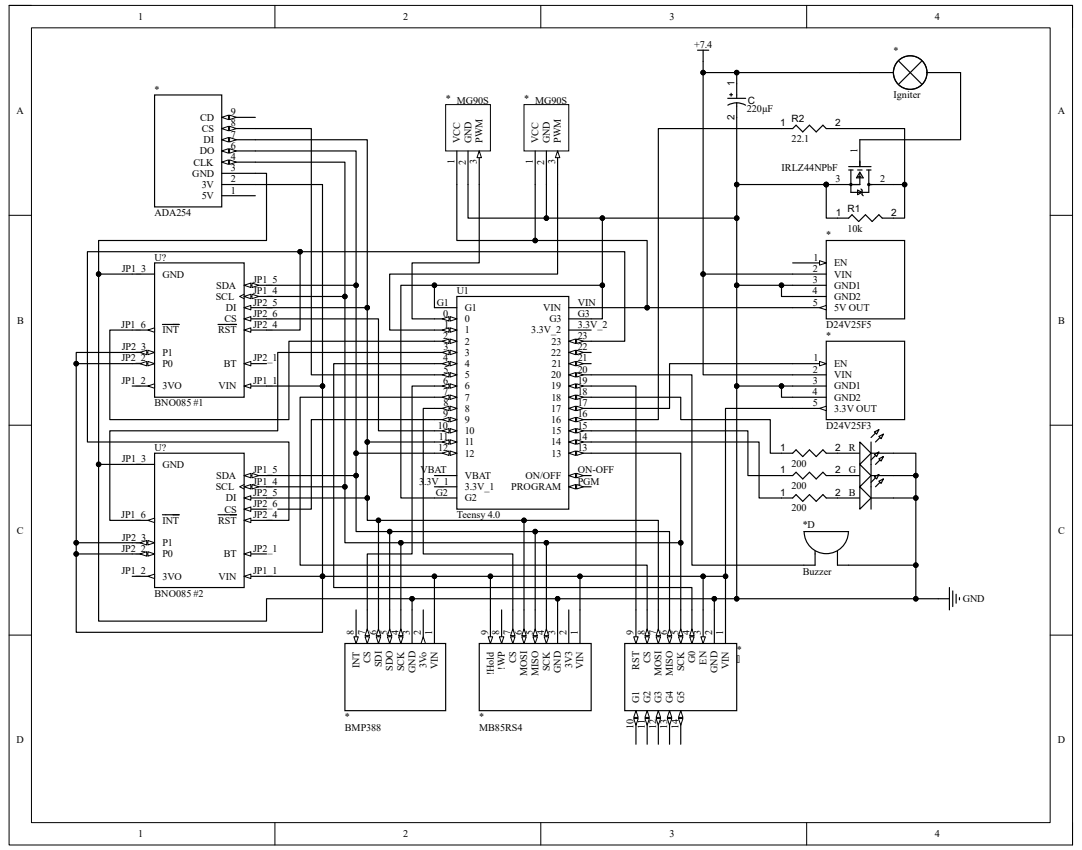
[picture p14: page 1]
VBAT VBAT 3.3V_1 3.3V_1 G2 G2; VIN; ON/OFF; ON-OFF; PROGRAM; PGM; Teensy 4.0; GND1; GND2; 3.3V OUT; 5V OUT; GND; RST; JP2_5 SCL; JP1_4 SDA; INT JP1_6; GND JP1_3; BNO085 #1; BNO085 #2; VIN ¹ 3V³ ² GND ³ SCK ⁴ MISO ⁵ MOSI 6 CS ⁷ !WP ⁸ !Hold 9 *; VIN ¹ GND ² EN ³ G⁰ ⁴ SCK ⁵ MISO ⁶ MOSI 7 CS ⁸ RST ⁹ G¹ 10 G² 11 G³ 12 G⁴ 13 G⁵ 14; IRLZ44NPbF; Igniter ¹ 2 220µF C; CLK; ADA254; VIN ¹ 3Vo 2 GND ³ SCK ⁴ SDO ⁵ SDI 6 CS ⁷ INT ⁸ *; BMP388; GRB; Buzzer

D24V25F5 VCC 1 GND 2 PWM 3 * MG90S VCC 1 GND 2 PWM 3 * MG90S

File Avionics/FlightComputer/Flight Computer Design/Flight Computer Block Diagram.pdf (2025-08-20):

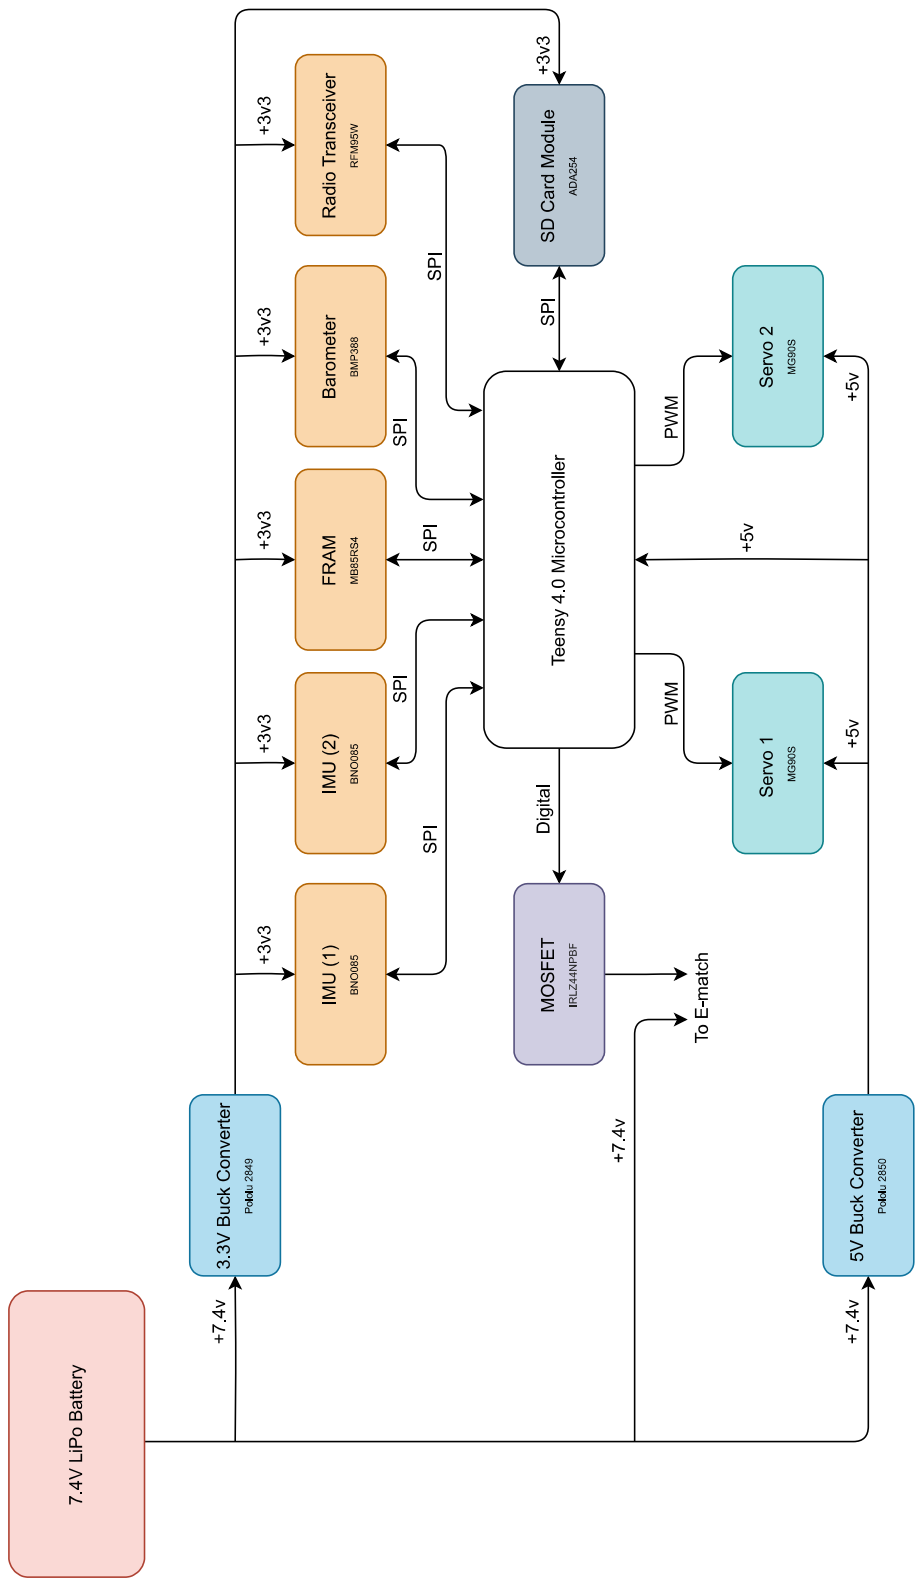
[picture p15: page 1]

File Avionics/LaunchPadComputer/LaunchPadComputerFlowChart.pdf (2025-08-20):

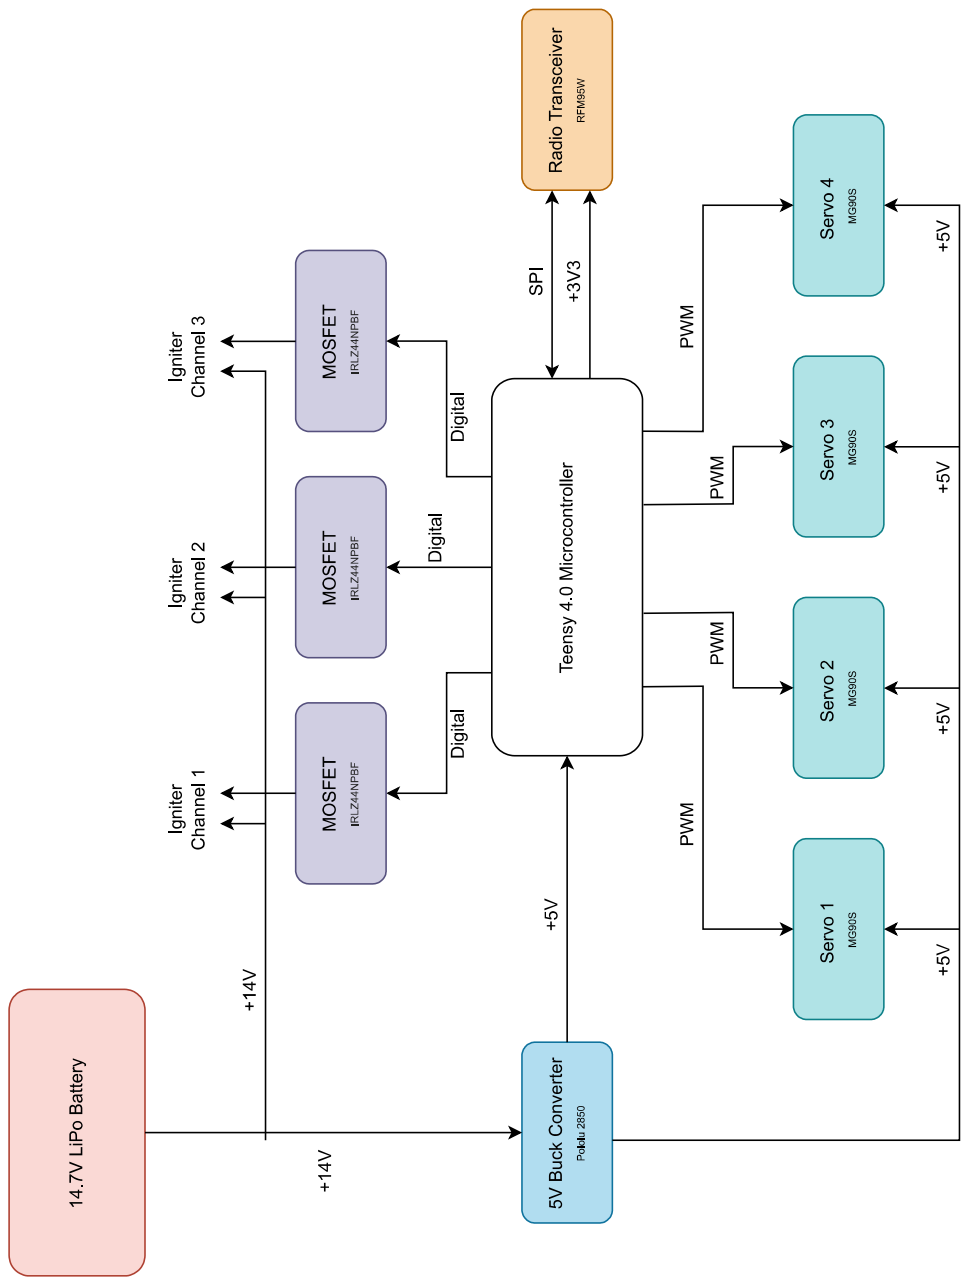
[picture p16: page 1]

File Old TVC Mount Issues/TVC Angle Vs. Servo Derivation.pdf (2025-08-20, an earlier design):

# Linear Approximation Derivation

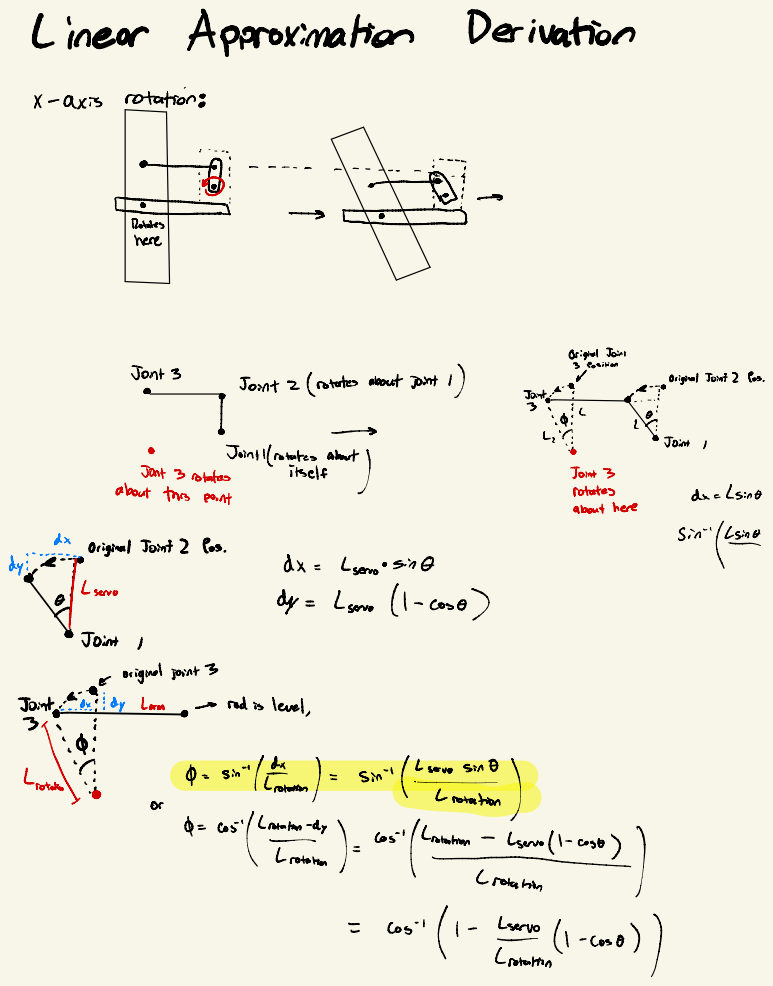
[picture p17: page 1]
X-axis; rotation:; here; Original Joint; Joint 3; Joint 2 (rotates about Joint 1); Joint t; 3 Position; · Joint I ⑨; Jont 3 rotates; itself; rotates; [sint; about here; Sinint; Lsero ·; Sin Q; Magical; Jointo; Lso (l-cost); dislevel,; sin" /Station) =

Original Joint 2 Pos.

Joint I/rotates about

about this point

Joint I
· Sini) sivo a =
cos() =
los
Cosi/1-ro(l-coo

## Nonlinear System Derivation

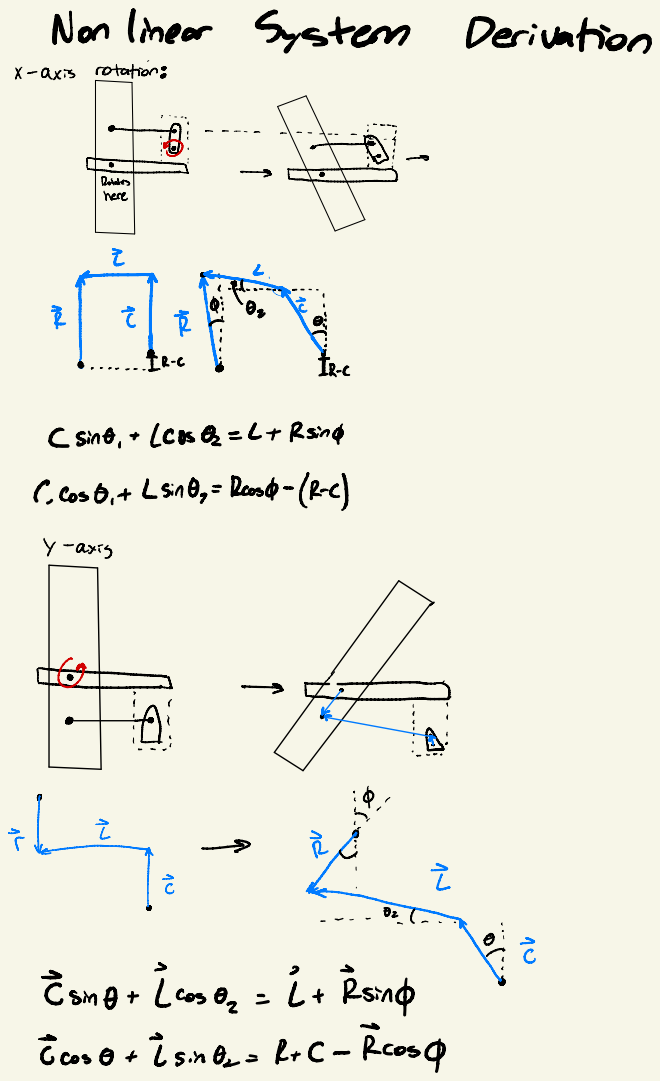
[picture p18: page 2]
X-axis; rotation:; 2 Cost+ (sinG,; = Rcosd- (R-c); Y-axis ·; · feI; -- -sint + [costz =; [ + Rsind; Ecost + [sinG=; R+C-Ecos&

(sint, + (Cos@z = L+ Rsind

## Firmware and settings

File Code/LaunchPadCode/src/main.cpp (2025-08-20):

#include <Arduino.h>
#include <setupIgniter.h>
#include <setupClampsServos.h>
#include <clampRelease.h>
#include <fireIgniter.h>
#include <Radio.h>

#define LED1_R 20
#define LED1_G 19
#define LED1_B 17

#define LED2_R 23
#define LED2_G 22
#define LED2_B 21

#define BUZZER_PIN 5

void setup() {
  Serial.begin(9600);
  delay(1000);
  pinMode(LED1_R, OUTPUT);
  pinMode(LED1_G, OUTPUT);
  pinMode(LED1_B, OUTPUT);
  pinMode(LED2_R, OUTPUT);
  pinMode(LED2_G, OUTPUT);
  pinMode(LED2_B, OUTPUT);
  digitalWrite(LED1_R, LOW);
  digitalWrite(LED1_G, LOW);
  digitalWrite(LED1_B, LOW);
  digitalWrite(LED2_R, LOW);
  digitalWrite(LED2_G, LOW);
  digitalWrite(LED2_B, LOW);

  setupIgniter();
  digitalWrite(LED1_B, HIGH);
  delay(1000);
  setupClampsServos();
  digitalWrite(LED2_B, HIGH); 

}

void loop() {
  if (radioAvailable()) {
    char buffer[32];
    int len = radioReceive((uint8_t*)buffer, sizeof(buffer) - 1);
    buffer[len] = '\0';

    if (strcmp(buffer, "PREP") == 0) {
      Serial.println("Received PREP from Ground Station");
      const char* ack = "ACK_PAD";
      radioSend((const uint8_t*)ack, strlen(ack));
    }

    if (strcmp(buffer, "LAUNCH") == 0) {
      Serial.println("Received LAUNCH Command. Starting Countdown...");

      for (int t = 1; t >= 0; t--) {
        digitalWrite(LED1_G, HIGH);
        digitalWrite(LED2_G, HIGH);
        tone(BUZZER_PIN,1000);
        delay(100);
        digitalWrite(LED1_G, LOW);
        digitalWrite(LED2_G, LOW);
        noTone(BUZZER_PIN);
        delay(900);
      }

      Serial.println("T-0: Releasing clamps and firing igniter!");
      releaseClamps();
      fireIgniter(1); //Fire igniter on channel 1
    }

    if (strcmp(buffer, "ABORT") == 0) {
      Serial.println("Received ABORT Command. Sending ACK.");
      const char* abortAck = "ACK_ABORT_PAD";
      radioSend((const uint8_t*)abortAck, strlen(abortAck));
    }
  }
}

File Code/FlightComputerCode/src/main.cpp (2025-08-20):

#include <Arduino.h>
#include <IgniterTest.h>
#include <BNO085_Print_Test.h>
#include <BMP388_Print_Test.h>
#include <Wire.h>
#include <Adafruit_BNO08x.h>
#include <FlashTest.h>
#include <LED_Test.h>
#include <SD_Test.h>
#include <Servos_test.h>
#include <radioTest.h>
#include <parachuteEjectionTest.h>
#include <servoCharacterization.h>
#include <servoResponseLag.h>
#include <servoLatency.h>


void setup(void) {
    Serial.begin(9600);
    delay(5000);
    setColor(0,255,0);
    testServos();
    

}


void loop() {
}
